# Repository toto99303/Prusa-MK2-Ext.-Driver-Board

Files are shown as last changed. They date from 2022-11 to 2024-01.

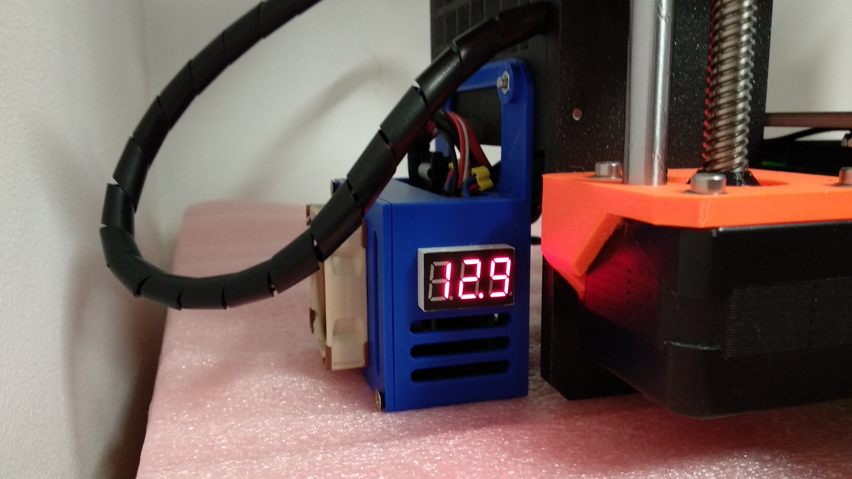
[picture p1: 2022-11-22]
Manuals/External driver board v2.4 (TMC2100, TMC2208, TMC2209))/high res pics/IMG_20180124_002903.jpg

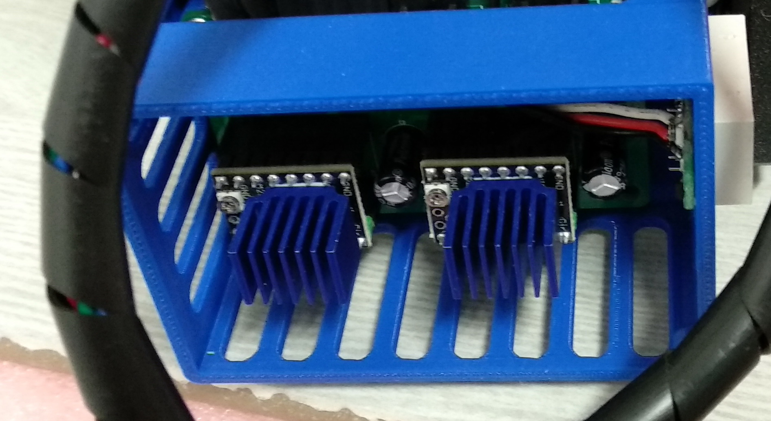
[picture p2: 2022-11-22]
Manuals/External driver board v2.1 with MK2.5/high res pics/drivers.jpg

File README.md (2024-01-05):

# Prusa-MK2-Ext.-Driver-Board
So, what is this? This is an external stepper driver board for X and Y stepper motors of the original Prusa MK2/MK2S/MK2.5/MK2.5S printers. It allows usage of TMC2100/TMC2208/TMC2209 drivers (Silent Step Stick and similar, (TMC2209 are recommended), so your printer will become a lot quieter and much smoother due to the 256 step interpolation (same as on the MK3). This is the latest upgraded version 2.4.1 of the board.  



More info here:  
https://vmod.wordpress.com/prusa-mk2s-ext-driver-board-v2-3/

BOM:

1 x wire-to-board header 3 POS 2.54MM(.100) (https://www.digikey.be/en/products/detail/cvilux-usa/CI3103P1V00-NH/13177511)

2 x 100uF 35V Capacitors (https://www.digikey.be/en/products/detail/rubycon/35ZLH100MEFC6-3X11/3134256)

2 x 10k through hole resistors (https://www.digikey.be/en/products/detail/stackpole-electronics-inc/RNF14BTE10K0/1682687)

1 x 2 way terminal block (https://www.tme.eu/en/details/dg306-5.0-2p12/pcb-terminal-blocks/degson-electronics/dg306-5-0-02p-12-00a-h/)

1 x right angle 2.54mm pin header 2x4 pins (https://jlcpcb.com/partdetail/Cvilux-CH81802H200/C918394)

2 x right angle dupont 1x4 MX2.54 TJC8 housing (https://vi.aliexpress.com/item/1005004362274135.html?gatewayAdapt=glo2vnm)

4 x driver header 1x8 2.54mm (https://grobotronics.com/pin-header-1x8-female-2.54mm.html?sl=en)

1 x IDC connector 2x4 wire-to-board connector (https://www.digikey.com/en/products/detail/cvilux-usa/CA2308PA10Z/15519128)

10-15cm short flat ribbon cable (https://www.digikey.com/en/products/detail/assmann-wsw-components/AWG28-16-G-300/655756)

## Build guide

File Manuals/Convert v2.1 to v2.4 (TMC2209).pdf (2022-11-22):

## Converting v2.1 to v2.4 and use TMC2209

When I created v2.1 there was no TMC2208 or TMC2209. It was designed for TMC2100.
That’s why you need to make some modifications to work with those.
I recommend buying TMC2209 in STANDALONE mode.

De-solder the jumpers (J_Y and J_X) on both boards and wire them as shown on the picture below:

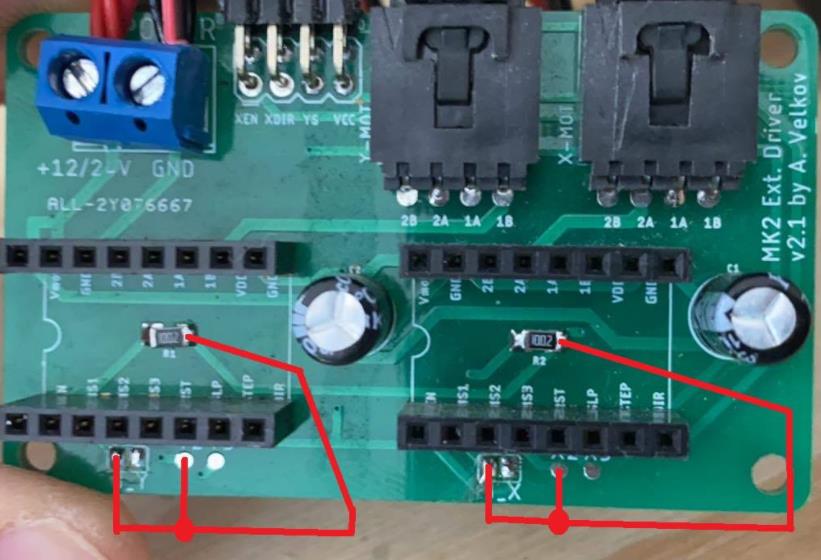
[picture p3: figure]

Be very careful and check everything with multimeter.
When done check for shorts between GND and VDC pin.

Next you need to cut the black cable connectors (Marked X Y Z etc.) from the gray data cable that go to mini-rambo and leave only the 8-pin connector going to the ext. driver board.
You will solder them to your mini-rambo later by the installation manual. They should look like this at the end:

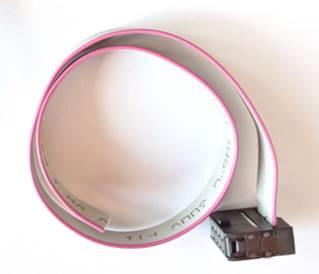
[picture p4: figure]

Next you need to follow the guide for v.2.4 here: https://drive.google.com/open?id=1o_A4ZHai253kLMRttBMnLbEIv-KRri8t

Also follow the manual for second board for Z axis if you have a second board.

One more important thing:

Most probably after plugging the board your motor axes will be inverted (X moving backwards instead of forward etc.).
If so you will need to swap the wires on each motor harness (X, Y). Use a needle and remove them carefully from the connector, swap them and plug them back:

So, we need to invert (switch) all wires on the X and Y motor connectors. Since connectors cannot be plugged in the opposite way you’ll have to use a small needle to pull all pins from the connectors and plug them back in reverse order:

### Original wiring: Left to right – Black, Green, Red, Blue

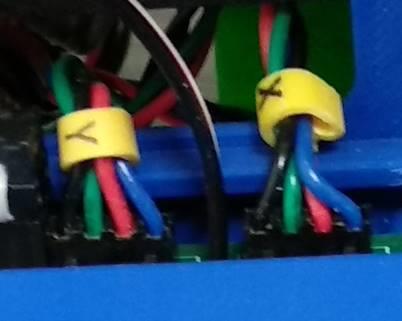
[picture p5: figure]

### New wiring: Left to right – Blue, Red, Green, Black

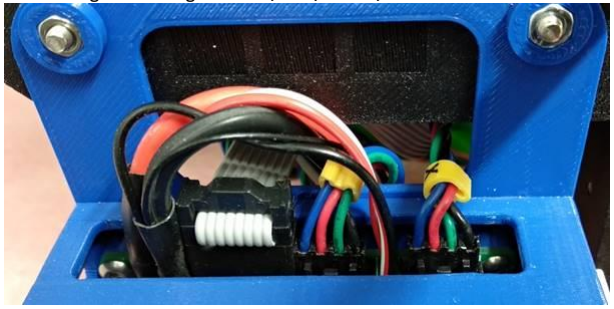
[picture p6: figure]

## Use needle here

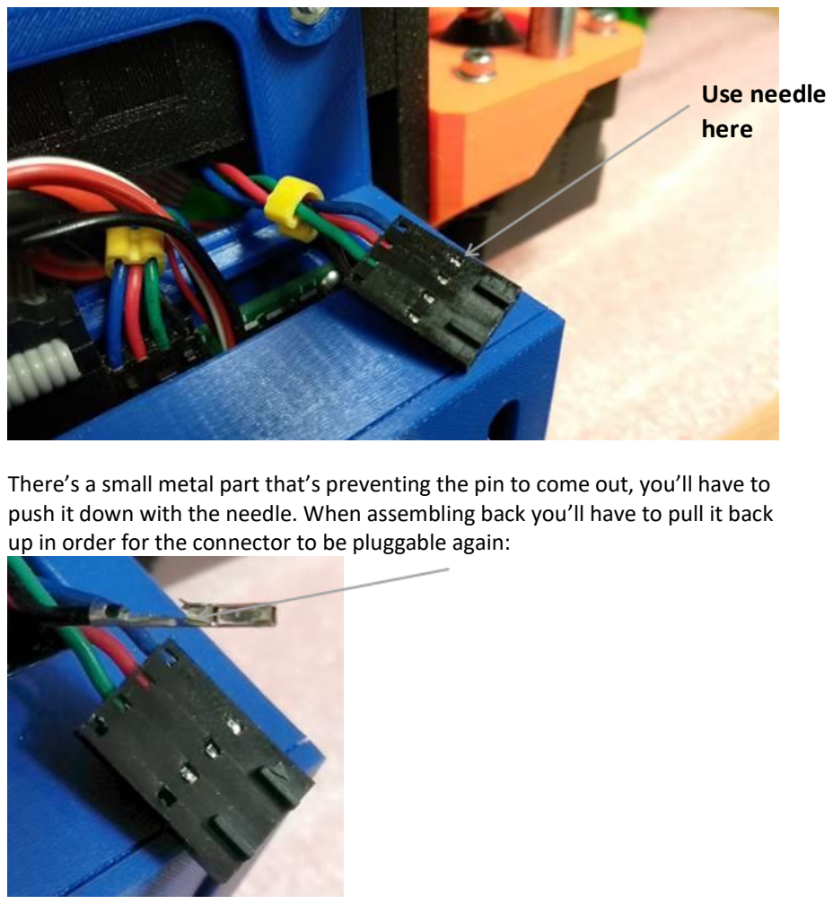
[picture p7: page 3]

### There’s a small metal part that’s preventing the pin to come out, you’ll have to push it down with the needle. When assembling back you’ll have to pull it back up in order for the connector to be pluggable again:

### Wire colors should look like this:

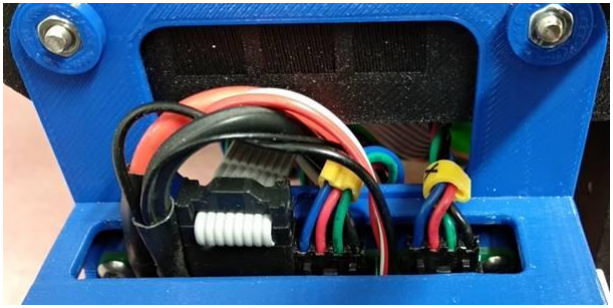
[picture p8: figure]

### That info should be enough for you to complete the mod with v2.1 and

TMC2209.

### Once again, read the manuals in advance, make a step-by-step plan and act

when ready and sure what you’re doing.

### I know it’s not an easy mod, but it’s worth it, believe me

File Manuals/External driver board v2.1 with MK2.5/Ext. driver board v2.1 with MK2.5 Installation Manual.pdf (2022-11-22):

## External Driver Board v2.1 with MK2.5 Installation Manual

Thanks for supporting this project! I’ll try to guide you as best as I can, but I will not go to the simple details as how to place the nuts on their place and put together a box, I assume you’re good enough to do this.

Ok, so you bought the old version of the ext. driver board (v2.1), but you want to install it with MK2.5 upgrade or any other current or future upgrade. This manual starts from the beginning but if you have it already installed you can skip some of the steps. Here’s two important things to know before proceeding with this mod:

1. By soldering on the back of your mini-rambo and changing motor connector pins you’re practically voiding your prusa warranty!
2. I take no responsibility if you mess this modification up and/or damage your printer. You need to have basic soldering skills. Do at your own risk, or get someone more experienced to do it for you!

Let’s start:
First you need to supply power to the board. You disassemble the original PSU plastic cover and take it out just a little up so you can connect the power leads to it:

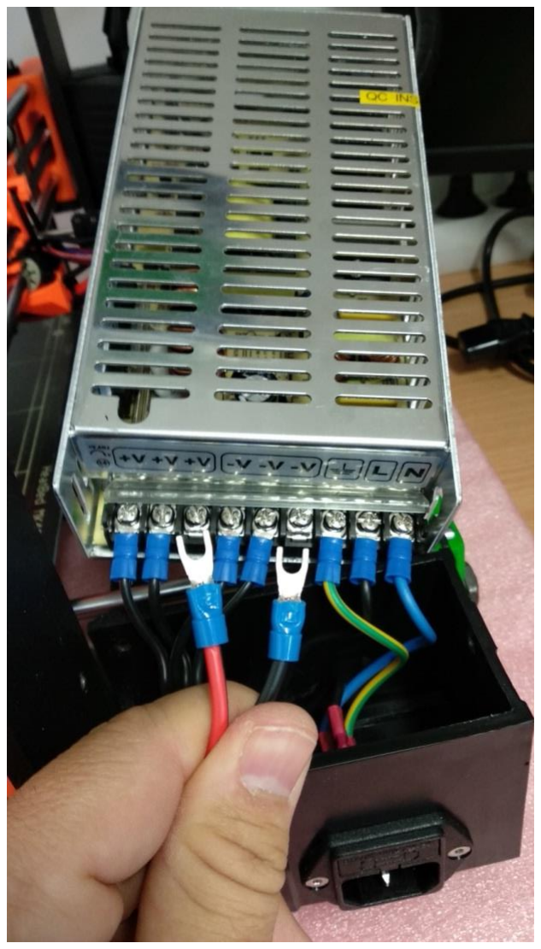
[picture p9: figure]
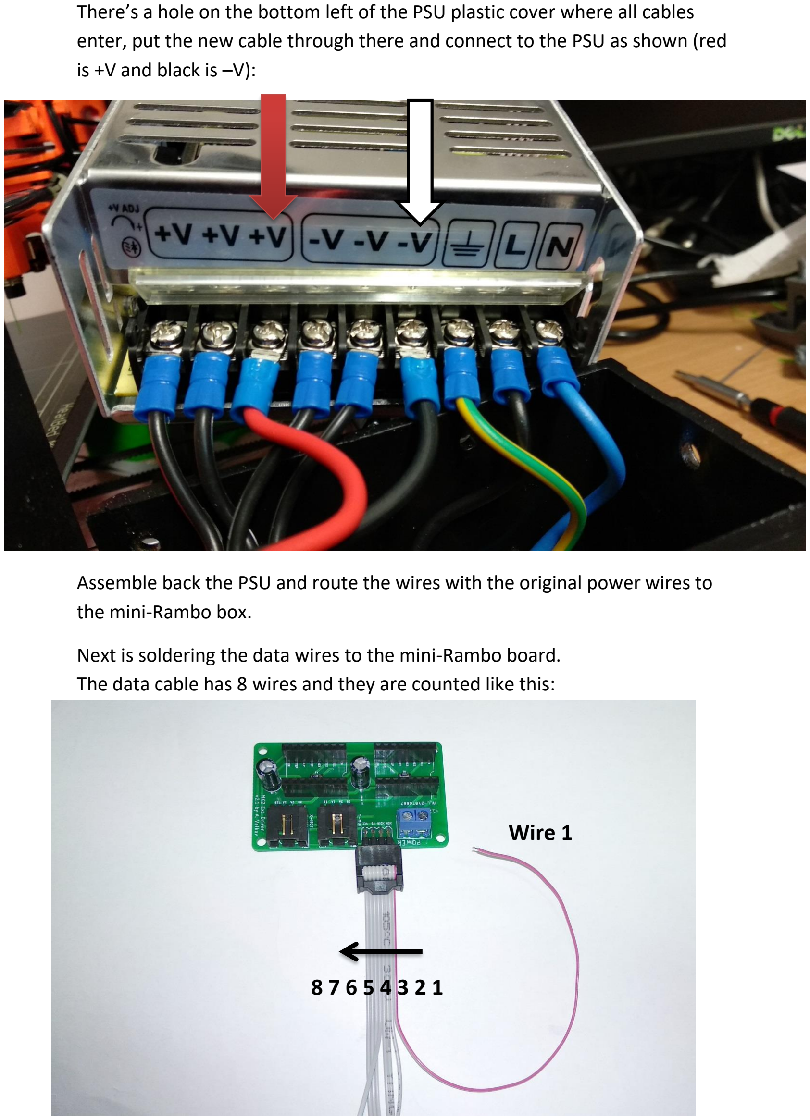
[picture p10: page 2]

There’s a hole on the bottom left of the PSU plastic cover where all cables enter, put the new cable through there and connect to the PSU as shown (red is +V and black is –V):

Assemble back the PSU and route the wires with the original power wires to the mini-Rambo box.

Next is soldering the data wires to the mini-Rambo board.
The data cable has 8 wires and they are counted like this:

8 7 6 5 4 3 2 1

Wire 1

Wires description:

The single wire on the side of the blue power connector is always wire number 1 (cable color could be red or grey)

1. X-EN - has to be soldered to XEN pad on the mini Rambo
2. X-STEP – has to be soldered to XSTEP pad on the mini Rambo
3. X-DIR – has to be soldered to XDIR pad on the mini Rambo
4. Y-EN – has to be soldered to YEN pad on the mini Rambo
5. Y-STEP - has to be soldered to YSTEP pad on the mini Rambo
6. Y-DIR - has to be soldered to YDIR pad on the mini Rambo
7. VCC - has to be soldered to +5V pad on the mini Rambo
8. GND - has to be soldered to GND pad on the mini Rambo

Unfortunately you will have to solder all 8 wires to the back of the mini-rambo.

In order to solder the wires you’ll have to unplug all cables and take the mini-rambo out of the box. Solder all wires on the back as shown below. (open the high res picture from the folder for clearer view)

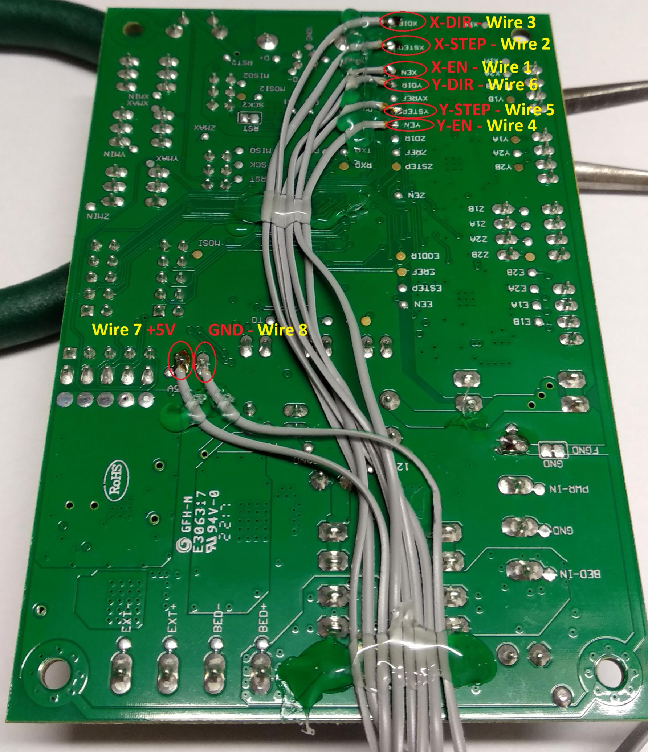
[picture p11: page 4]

Route all wires down and secure them with some hot silicone. This will prevent cutting the wires from vibrations etc.

You can now assemble the mini-rambo back in the original box with all cables plugged back (except for X and Y motor cables). Replace the bottom two screws with longer ones, remove the nuts from the original box and place them on the Ext. driver board box. (I assume you have printed it, https://www.thingiverse.com/thing:2777899) Assemble the external driver board in the new box and secure the box to the original box with the two longer screws. (note: If you’re installing a voltmeter place it first before the external board, otherwise it won’t be possible later) You should now have all data wires soldered, mini-rambo back in place with all cables plugged and the new box secured on the outside.

Now there’s one more thing you need to do. The new stepper drivers (TMC2100) have their motor direction naturally reversed with regards to the old drivers on the mini-rambo. So there’s two ways to fix this:

1. Use the original motor connector wiring and recompile the original prusa firmware with INVERT_X_DIR and INVERT_Y_DIR both set to “true” (located in Configuration.h)
2. Physically reverse the pins on the X and Y motor connectors and use the original untouched prusa firmware.

So for the first option, if you got this far you should already know how to compile and flash your own custom firmware. If not, let me know so I can send you the current re-compiled firmware for MK2.5 .

We’ll continue with the second option.

So, we need to invert (switch) all wires on the X and Y motor connectors. Since connectors cannot be plugged in the opposite way you’ll have to use a small needle to pull all pins from the connectors and plug them back in reverse order: Original wiring: Left to right – Black, Green, Red, Blue

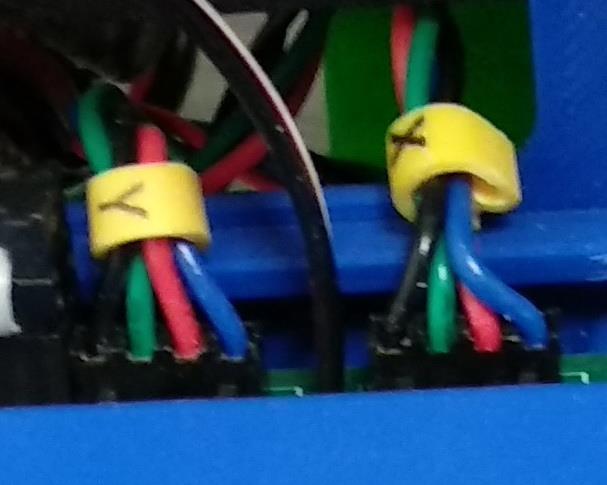
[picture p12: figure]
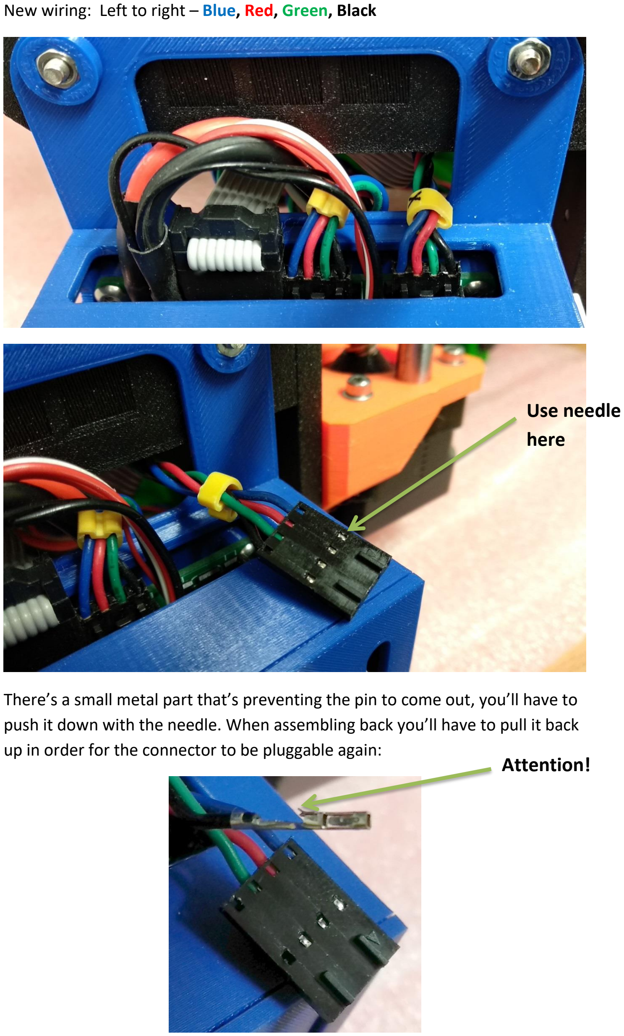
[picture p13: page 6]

New wiring: Left to right – Blue, Red, Green, Black

There’s a small metal part that’s preventing the pin to come out, you’ll have to push it down with the needle. When assembling back you’ll have to pull it back up in order for the connector to be pluggable again:

Use needle
here

Attention!

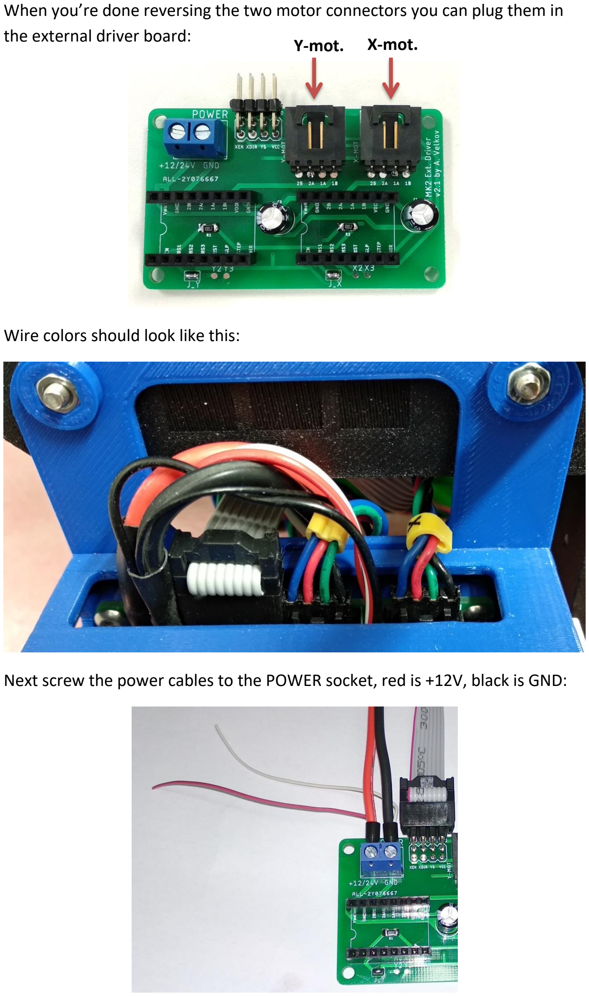
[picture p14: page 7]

When you’re done reversing the two motor connectors you can plug them in the external driver board:

Wire colors should look like this:

Next screw the power cables to the POWER socket, red is +12V, black is GND:

Y-mot. X-mot.

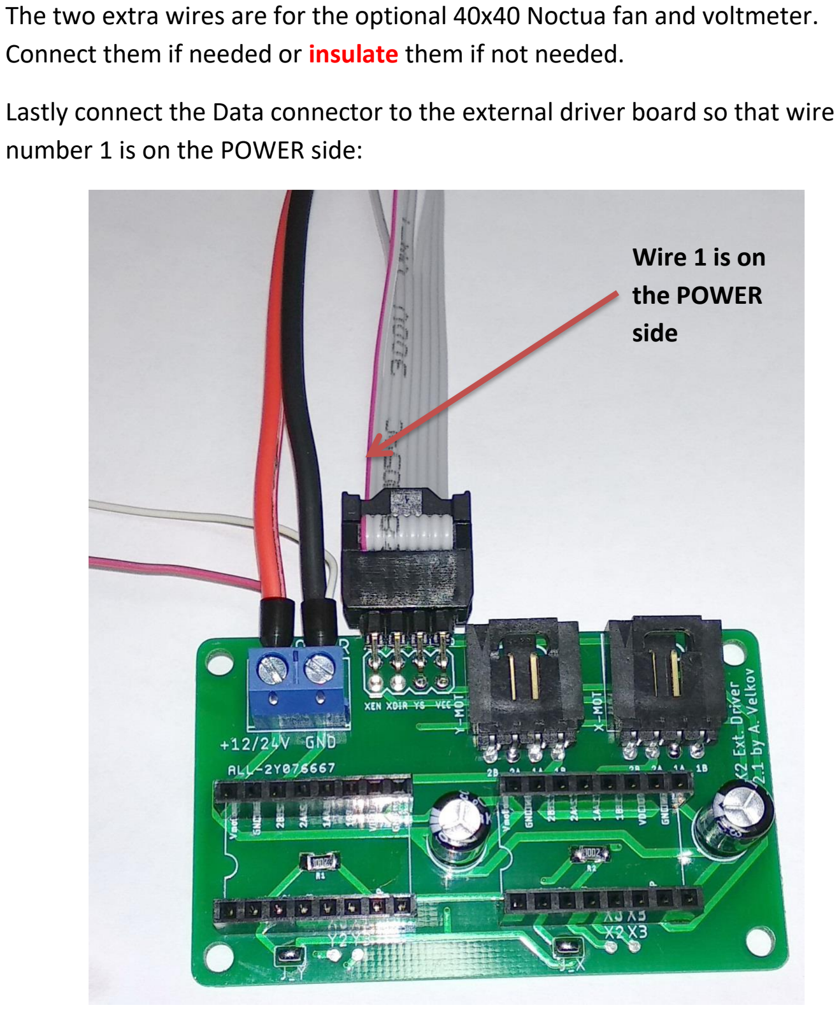
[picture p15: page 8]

The two extra wires are for the optional 40x40 Noctua fan and voltmeter. Connect them if needed or insulate them if not needed.

Lastly connect the Data connector to the external driver board so that wire number 1 is on the POWER side:

Wire 1 is on
the POWER
side

Now that you have all the wiring done you can plug the TMC2100 drivers to their places oriented with the pot trimmer on the left side:

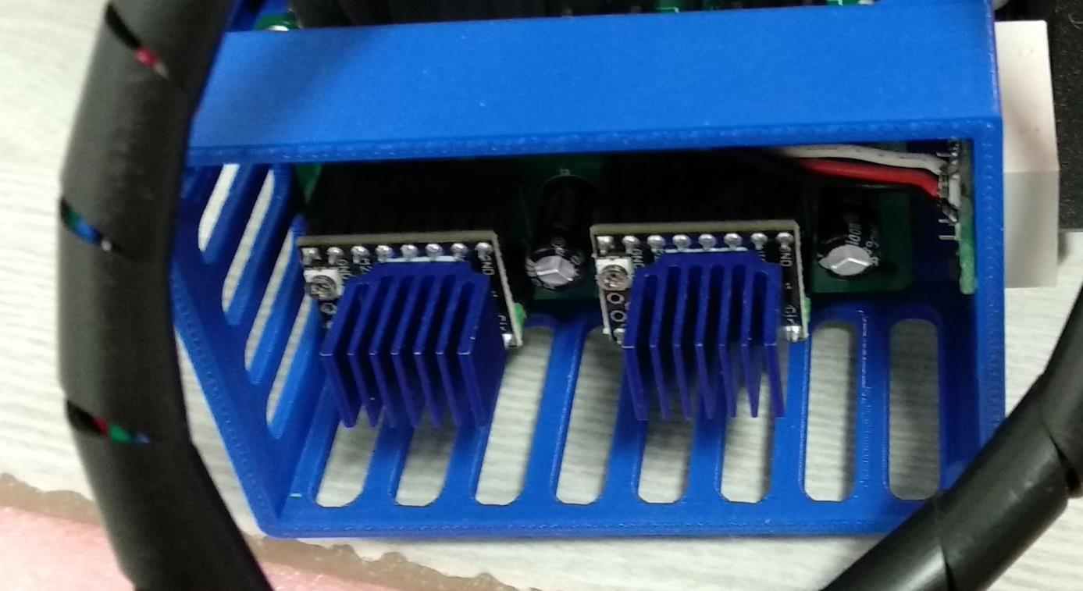
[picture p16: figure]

Check all wiring again before turning the printer on. Place bigger heatsinks if available on the drivers.

After powering on don’t rush to print, follow this first:

1. Check X and Y motors movement directions (Settings -> Move axis). Move them from the menu one by one. Are directions correct?
2. Check if “Disable steppers” is working fine.
3. Now you have to set Vref on the drivers, but it depends on what bearings you have on your Prusa. If you have LM8UU original bearings set Vref to 0.81V. If you use IGUS I recommend to set Vref to 1V or replace them back with the original metal ones, because IGUS will cause more friction and may cause layer shifting…
4. Set the Vref voltages on both drivers to 0.81 V with multimeter, here’s how:
- Put the multimeter to small DC voltage range (2 – 5 volts, etc.)
- Place the Black lead to GND on the POWER socket.
- Place the Red lead to the pot center or at the Vref pin if your driver has the pot on the bottom side.
- Rotate the pot with plastic screwdriver slowly clockwise so that voltage gets to 0.81 V. Stepper motors will get hot during print, but this seems to be normal for the TCM2100 drivers. Using plastic screwdriver will ensure you’re not going to short anything. I’ve already burned one driver with metal screwdriver…
5. Do XYZ calibration, and first layer calibration. (http://www.youtube.com/watch?v=JqH41K2vq0g&t=9m50s)

X and Y stepper movement should be normal and quieter than before.

Note that if you purchased original Watterott drivers they are configured by default for 1/16th SpreadCycle mode via the two jumpers on my board. You will probably hear whining or hissing in this mode.

To get the 1/16th StealthChop (silent) mode you have to desolder the X and Y jumpers here:

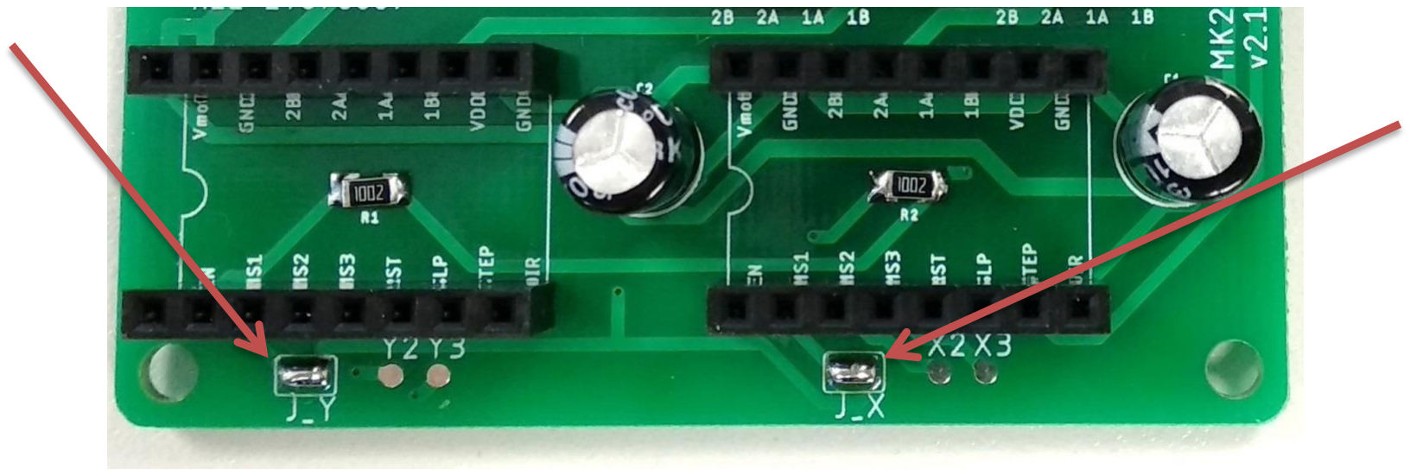
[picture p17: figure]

This is only for the original Watterott drivers.

If you purchased chinese clone drivers (MKS etc., black PCB) you’ll be already running in 1/16th StealthChop mode as those have their CGF pins floating and they are not affected by the jumpers on my board.

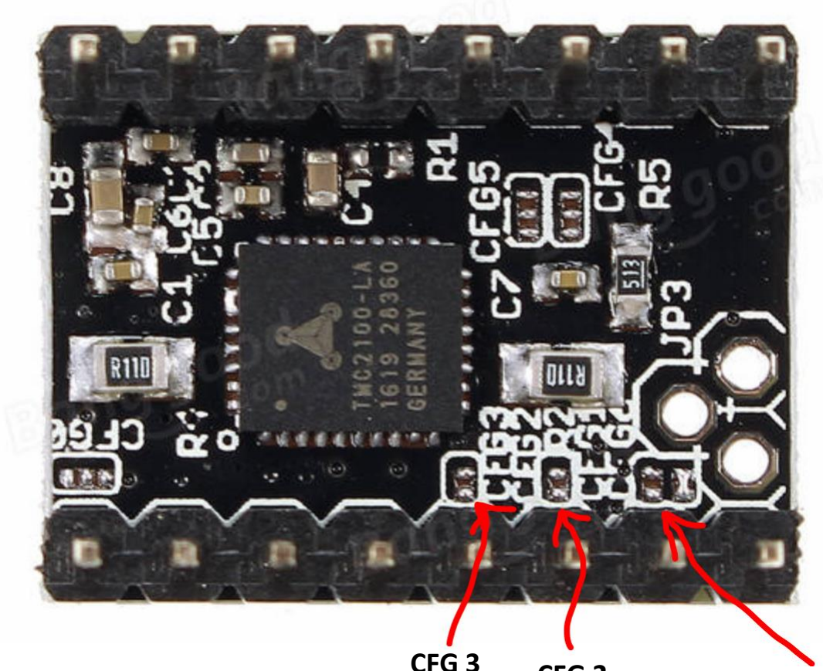
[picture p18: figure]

CFG 3 | CFG 2 | CFG 1

You can read more about this here: https://vmod.wordpress.com/2018/05/02/important-news-about-the-tmc2100-drivers/ (https://vmod.wordpress.com/2018/05/02/important-news-about-the-tmc2100-drivers/)

Before making the first print assemble the box cover with the optional Noctua fan. Cooling the drivers will be your second assurance for normal operation and no layer shifting.

Finally – enjoy your new silent MK2.5 printer! Happy printing!

Basic troubleshooting:

1. If X or Y motors are not moving you have a couple of reasons why:
- Check connection of wire 2 for X and wire 5 for Y.
- Check connection of wire 1 for X and wire 4 for Y.
- There’s no power to the external board, check the voltage on the power socket with multimeter (Red lead to 12V and Black to GND).
- There’s no 5V power to the stepper drivers, check wires 7 and 8. check the voltage between them with multimeter, should read 5V)
- Vref is too low. Set Vref according to the manual above.
- The stepper driver is faulty. I’ve seen this with some chinese clones. Turn the printer off and swap the two TMC2100s. If now the other axis is not moving then you have either wiring problem or driver is faulty.
2. “Disable steppers” is not working:
- Check connection of wire 1 for X and wire 4 for Y
3. Motor is moving only in one direction despite what you command from the LCD:
- Check connection of wire 3 for X and wire 6 for Y
4. XYZ calibration fails:
- Increase Vref with 0.5V on both stepper drivers. Repeat if it appears again.
5. Layer shift in X or Y axis:
- Check for hard movement on both directions.
- Increase Vref with 0.5V on the affected axis stepper driver. Repeat if it appears again.

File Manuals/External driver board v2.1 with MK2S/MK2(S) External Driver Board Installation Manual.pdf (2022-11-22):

## MK2(S) External Driver Board

## Installation Manual

Detailed features and description can be found on the blog page here: https://vmod.wordpress.com/prusa-mk2s-ext-driver-board/

Thanks for supporting this project! I’ll try to guide you as best as I can, but I will not go to the simple details as how to place the nuts on their place and put together a box, I assume you’re good enough to do this.

Let’s start:
First you need to supply power to the board. You disassemble the original PSU plastic cover and take it out just a little up so you can connect the power leads to it:

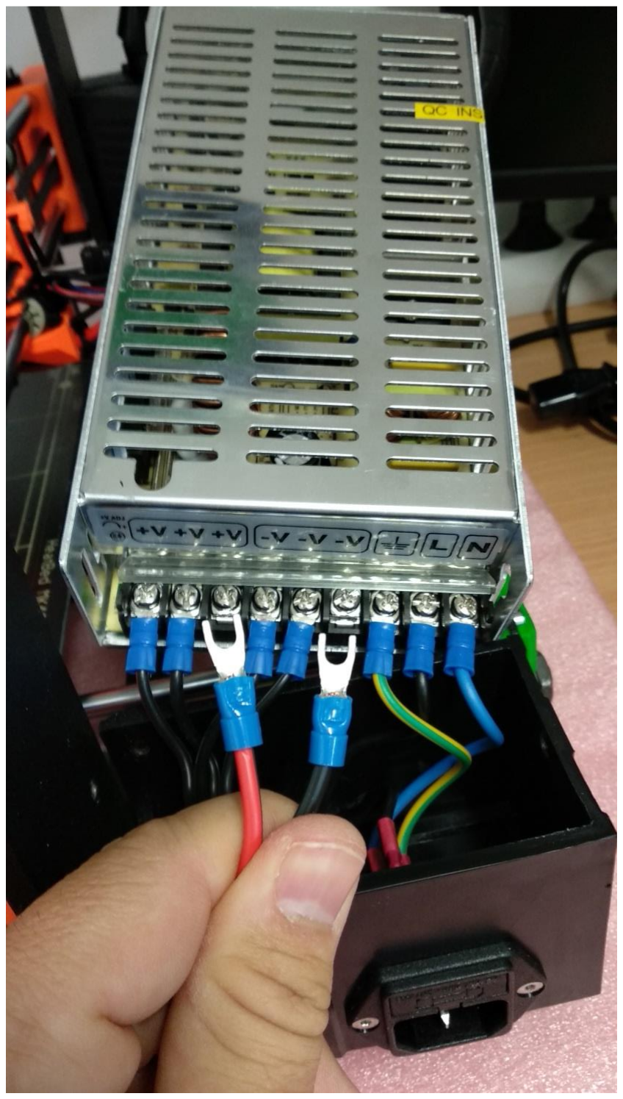
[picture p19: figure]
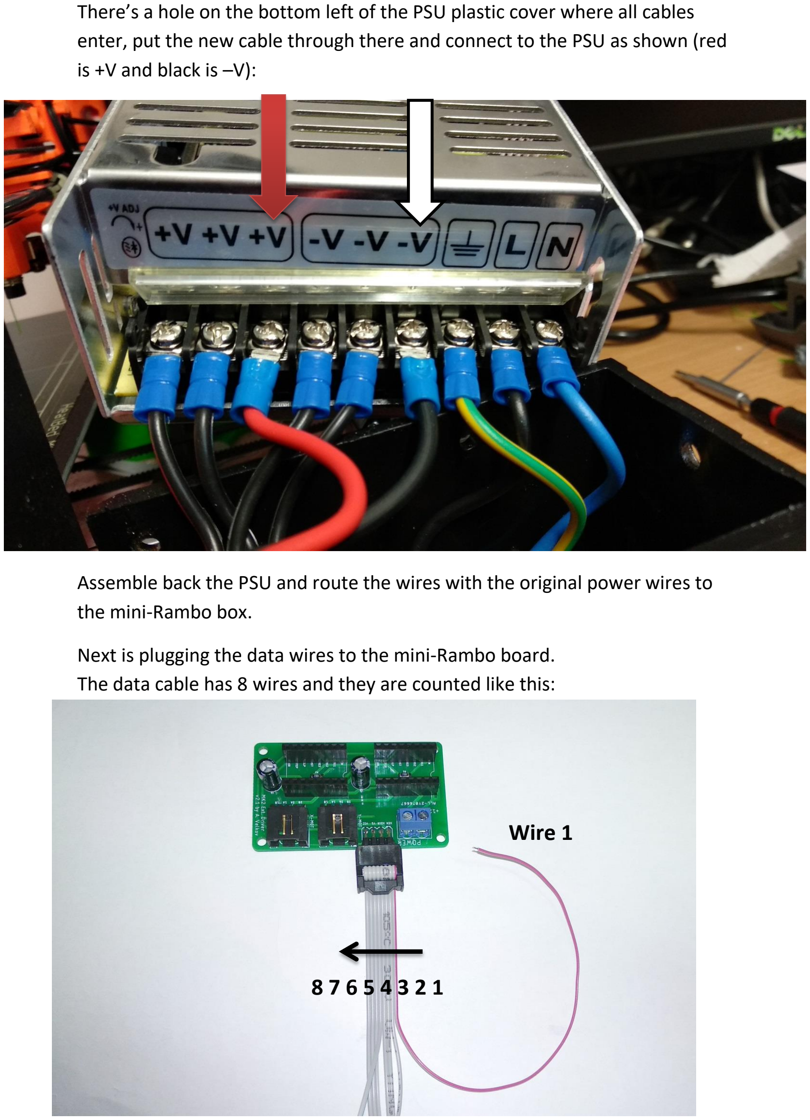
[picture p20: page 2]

There’s a hole on the bottom left of the PSU plastic cover where all cables enter, put the new cable through there and connect to the PSU as shown (red is +V and black is –V):

Assemble back the PSU and route the wires with the original power wires to the mini-Rambo box.

Next is plugging the data wires to the mini-Rambo board.
The data cable has 8 wires and they are counted like this:

8 7 6 5 4 3 2 1

Wire 1

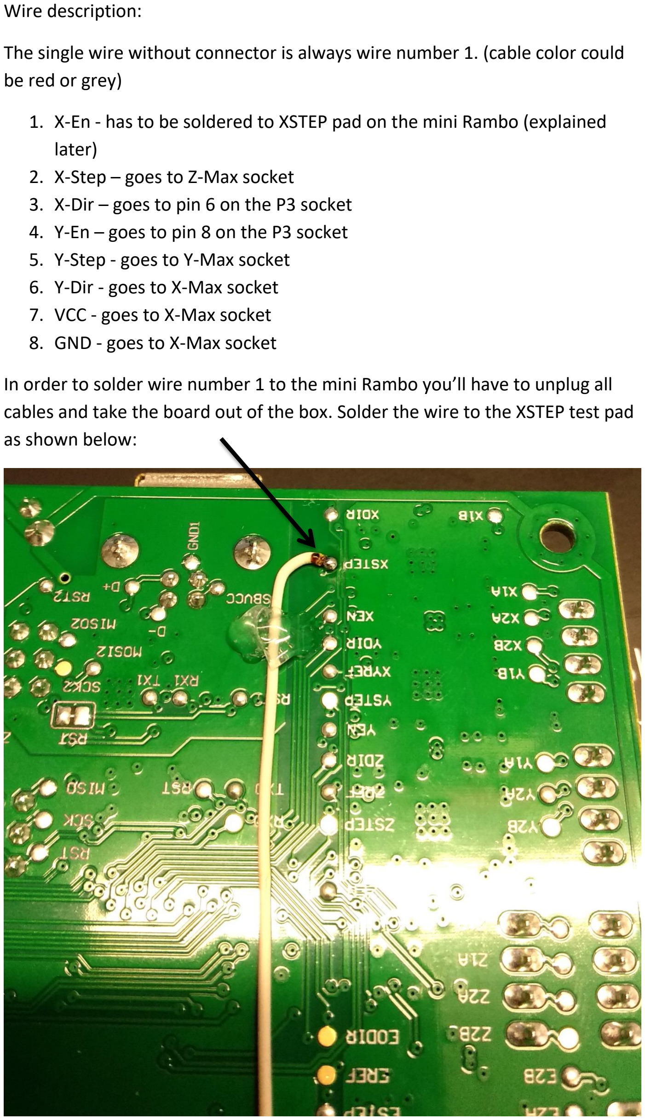
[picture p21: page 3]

Wire description:

The single wire without connector is always wire number 1. (cable color could be red or grey)

1. X-En - has to be soldered to XSTEP pad on the mini Rambo (explained later)
2. X-Step – goes to Z-Max socket
3. X-Dir – goes to pin 6 on the P3 socket
4. Y-En – goes to pin 8 on the P3 socket
5. Y-Step - goes to Y-Max socket
6. Y-Dir - goes to X-Max socket
7. VCC - goes to X-Max socket
8. GND - goes to X-Max socket

In order to solder wire number 1 to the mini Rambo you’ll have to unplug all cables and take the board out of the box. Solder the wire to the XSTEP test pad as shown below:

Route the wire down and secure it with some hot silicone. This will prevent cutting the wire from vibrations etc:

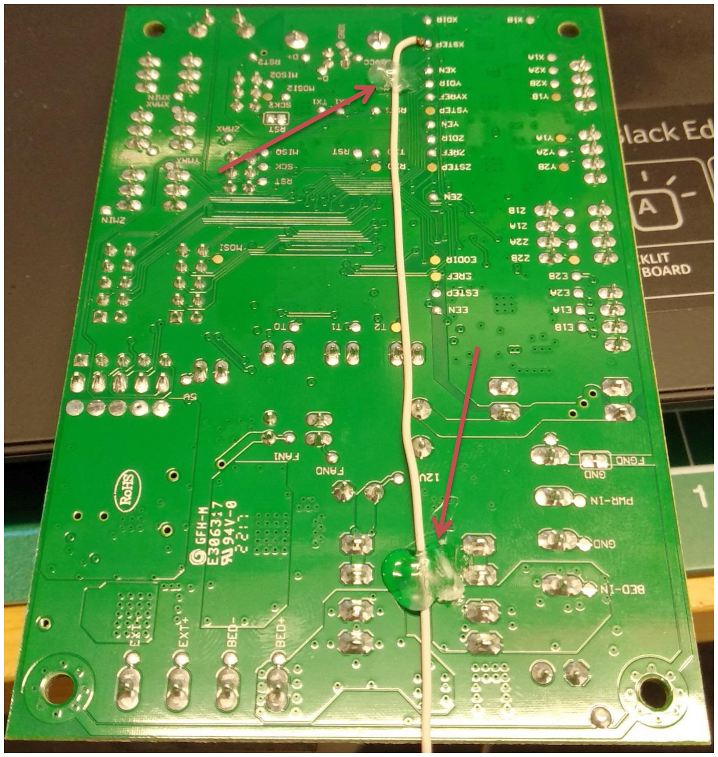
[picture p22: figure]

You can now assemble the mini-rambo back in the original box with all cables plugged back (except for X and Y motor cables). Replace the bottom two screws with longer ones, remove the nuts from the original box and place them on the Ext. driver board box. (I assume you have printed it, https://www.thingiverse.com/thing:2777899) Assemble the external driver board in the new box and secure the box to the original box with the two longer screws. (note: If you’re installing a voltmeter place it first before the external board, otherwise it won’t be possible later) You should now have wire number 1 soldered, mini-rambo back in place with all cables plugged and the new box secured on the outside with no cables plugged to the external driver board. We’ll plug them later.

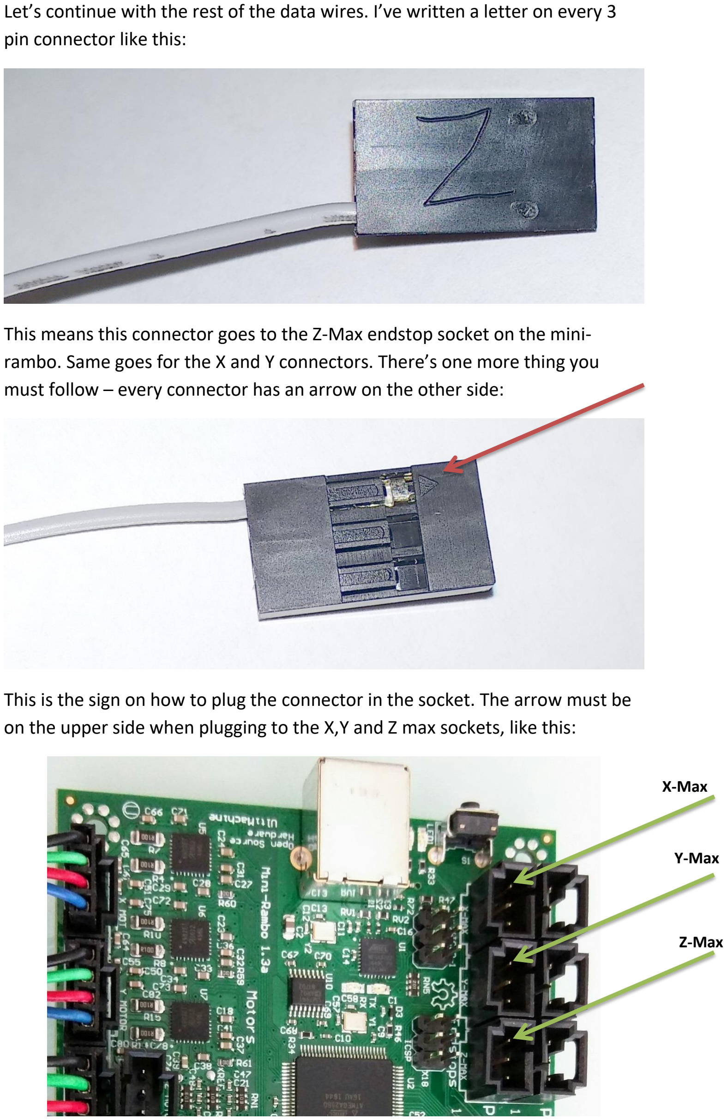
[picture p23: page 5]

Let’s continue with the rest of the data wires. I’ve written a letter on every 3 pin connector like this:

This means this connector goes to the Z-Max endstop socket on the mini-rambo. Same goes for the X and Y connectors. There’s one more thing you must follow – every connector has an arrow on the other side:

This is the sign on how to plug the connector in the socket. The arrow must be on the upper side when plugging to the X,Y and Z max sockets, like this:

X-Max

Z-Max

Y-Max

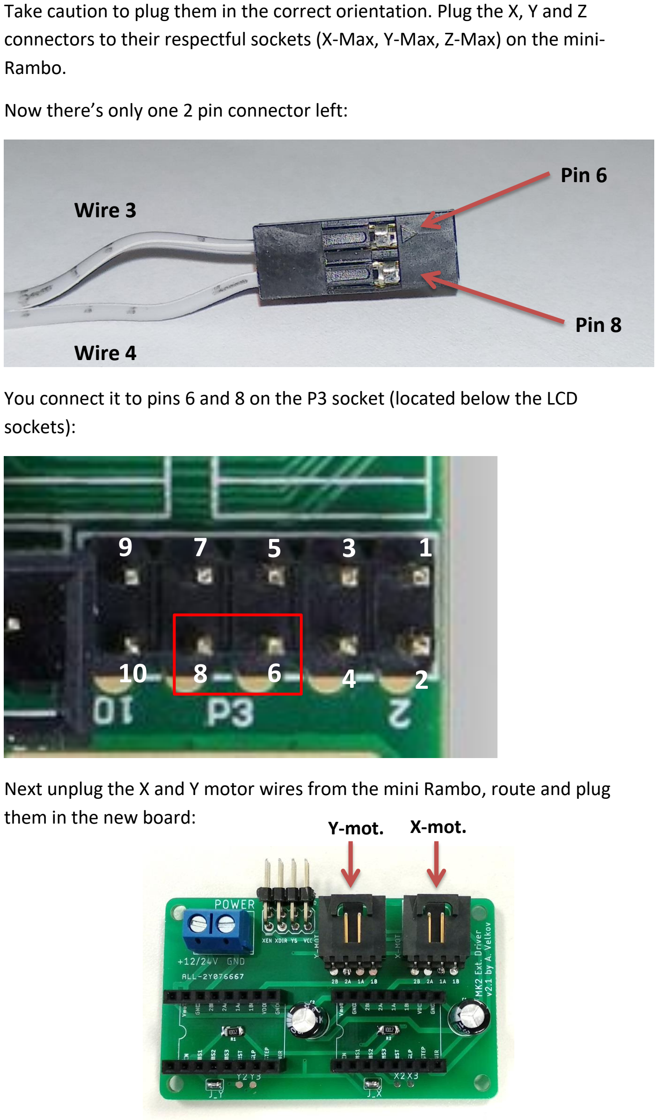
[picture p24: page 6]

Take caution to plug them in the correct orientation. Plug the X, Y and Z connectors to their respectful sockets (X-Max, Y-Max, Z-Max) on the mini-Rambo.

Now there’s only one 2 pin connector left:

You connect it to pins 6 and 8 on the P3 socket (located below the LCD sockets):

Next unplug the X and Y motor wires from the mini Rambo, route and plug them in the new board:

Wire 3

Wire 4

Pin 6

Pin 8

9 | 7 | 5 | 3 | 1

6 4
10 | 8 | 2
Y-mot. | X-mot.

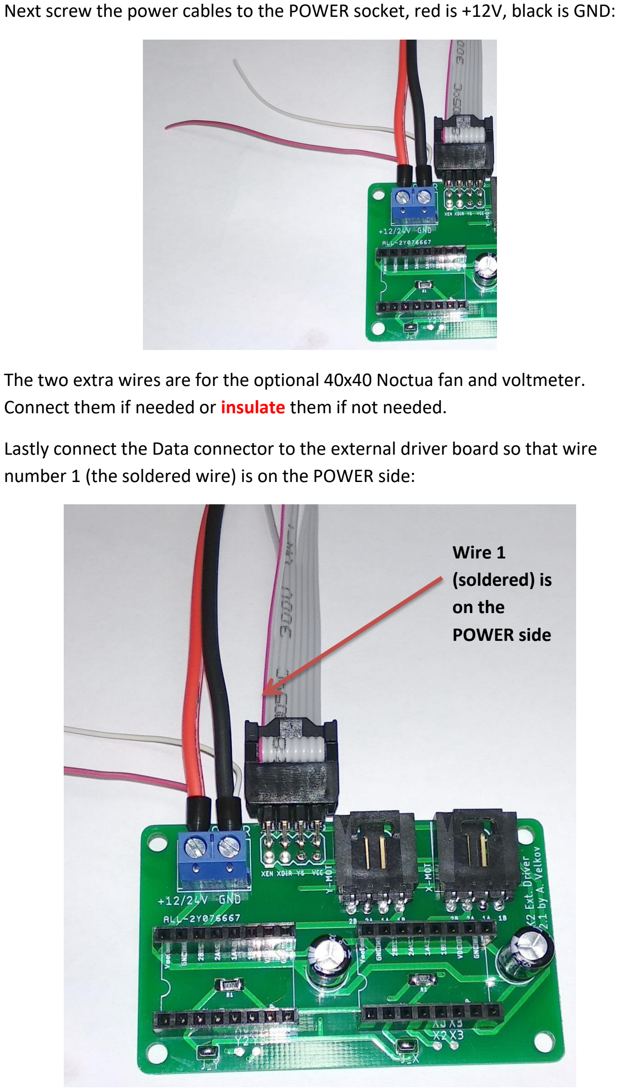
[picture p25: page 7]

Next screw the power cables to the POWER socket, red is +12V, black is GND:

The two extra wires are for the optional 40x40 Noctua fan and voltmeter. Connect them if needed or insulate them if not needed.

Lastly connect the Data connector to the external driver board so that wire number 1 (the soldered wire) is on the POWER side:

Wire 1
(soldered) is
on the
POWER side

Now that you have all the wiring done you can plug the TMC2100 drivers to their places oriented with the pot trimmer on the left side:

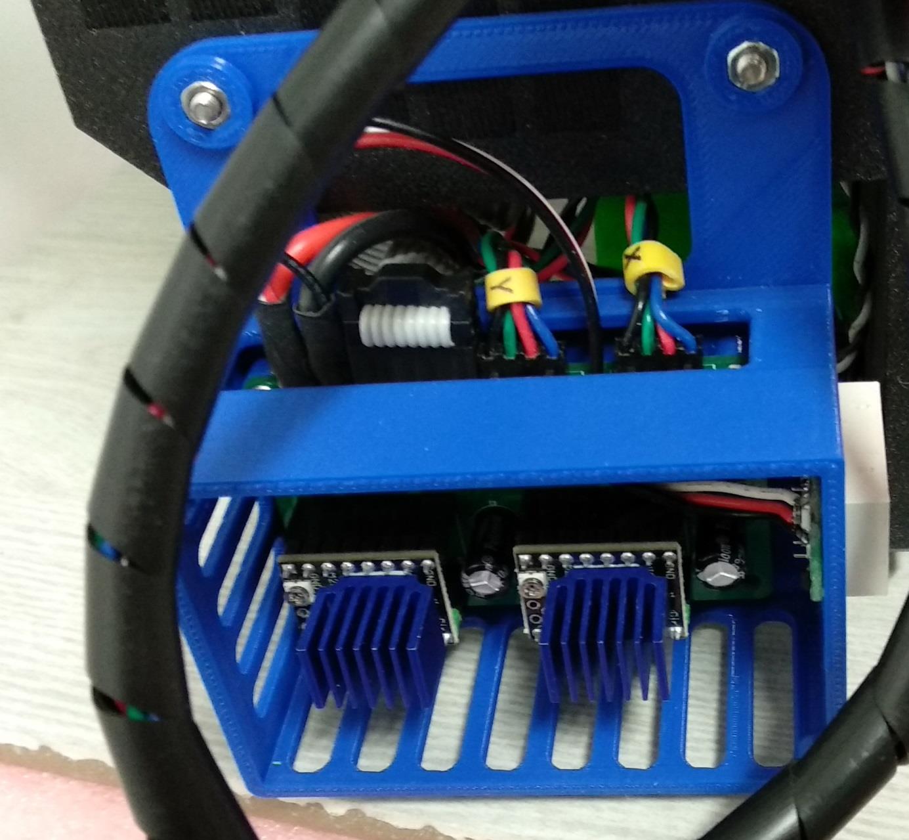
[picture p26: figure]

Everything should look like on the picture above. Check all wiring again before turning on the printer. Place bigger heatsinks if available on the drivers.

Now we’re ready to flash the modified firmware to the mini-Rambo. Download the ZIP file with the firmware from here (currently v3.1.0): https://drive.google.com/file/d/1ZUJ4TQwXW29yG_LHIU8oj9F0EPkxLeVB/view?usp=sharing (https://drive.google.com/file/d/1ZUJ4TQwXW29yG_LHIU8oj9F0EPkxLeVB/view?usp=sharing)

Inside you’ll find the original firmware for MMU and the standard printer and the modified ones for the external driver board. Turn on the printer and upload the desired firmware (in our case: 1_75mm_MK2-RAMBo13a-E3Dv6full_Ext_Driver_Board.hex) with the original Prusa Firmware Updater tool. You can follow the Prusa guide here (from Step 4):

http://help.prusa3d.com/l/en/article/r5ByKgVm69-firmware-upgrade-andflashing (http://help.prusa3d.com/l/en/article/r5ByKgVm69-firmware-upgrade-and-flashing)

After successful update don’t rush to print, follow this first:

1. Check X and Y motors movement directions (Settings -> Move axis). Move them from the menu one by one. Are directions correct?
2. Check if “Disable steppers” is working fine.
3. Set the Vref voltages on both drivers to 1V with multimeter, here’s how:
- Put the multimeter to small DC voltage range (2 – 5 volts, etc.)
- Place the Black lead to GND on the POWER socket.
- Place the Red lead to the pot center or at the Vref pin if your driver has the pot on the bottom side.
- Rotate the pot with plastic screwdriver so that voltage is 1V. I run mine at this voltage. Stepper motors will get hot during print, but this seems to be normal for the TCM2100 drivers. Using plastic screwdriver will ensure you’re not going to short anything. I’ve already burned one driver with metal screwdriver…
4. Do XYZ calibration, and first layer calibration. (http://www.youtube.com/watch?v=JqH41K2vq0g&t=9m50s)

X and Y stepper movement should be normal and quieter than before. The two drivers are configured by default for 1/16th SpreadCycle mode, which is the recommended one.

If you want to experiment you can turn on the 1/16th StealthChop mode by desoldering the X and Y jumpers here:

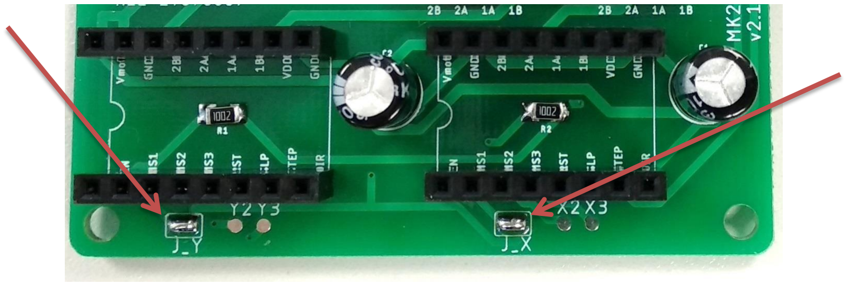
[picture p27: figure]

This will make it even quieter but will reduce the motor current and you might experience layer shifting. I don’t recommend this mode.

Before making the first print assemble the box cover with the optional Noctua fan. Cooling the drivers will be your second assurance for normal operation and no layer shifting.

Finally – enjoy your new silent MK2(S) printer! Happy printing!

Basic troubleshooting:

1. If X or Y motors are not moving you have a couple of reasons why:
- You have placed a connector the wrong way at the mini-rambo. Remember that the arrow on the connector should be on the upper side of the socket. Check again.
- There’s no power to the external board, check the voltage on the power socket with multimeter (Red lead to 12V and Black to GND).
- Vref is too low. Set Vref according to the manual above.
- The stepper driver is faulty. I’ve seen this with some chinese clones. Turn the printer off and swap the two TMC2100s. If now the other axis is not moving then you have either wiring problem or driver is faulty.
2. “Disable steppers” is not working:
- Check connection of wire 1 for X and wire 4 for Y
3. Motor is moving only in one direction despite what you command from the LCD:
- Check connection of wire 3 for X and wire 6 for Y

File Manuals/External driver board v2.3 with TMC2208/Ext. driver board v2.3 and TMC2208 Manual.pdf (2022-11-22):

## MK2(S) External Driver Board TMC2208 Installation Manual

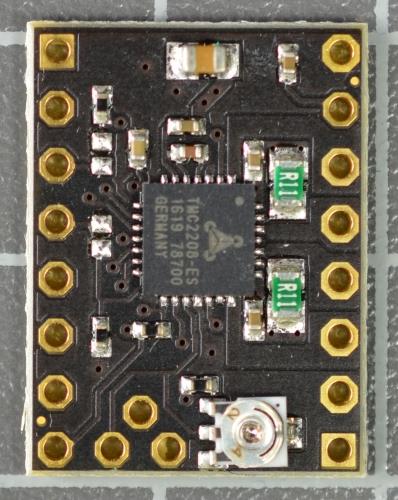
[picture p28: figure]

So, why using TMC2208? Mainly because:

stealthChop2™ No-noise, high-precision chopper algorithm for inaudible motion and inaudible standstill of the motor. Allows faster motor acceleration and deceleration than stealthChop™ and extends stealthChop to low stand still motor currents.
Benefits of using stealthChop2:
- Significantly improved microstepping with low cost motors
- Motor runs smooth and quiet
- Absolutely no standby noise
- Reduced mechanical resonance yields improved torque
- Reduced motor working temperature

Links:
https://www.watterott.com/index.php?page=product&info=5089 (without soldered pins)
https://www.watterott.com/en/SilentStepStick-TMC2208-with-Pins (with soldered pins)
https://www.watterott.com/en/Heatsink-9-x-9-x-12 (heatsinks)

Remark: the drivers from Watterott are being sold without heatsinks. You’ll have to buy them seperately.

WARNING!! I take no responsibility if you mess this modification up and/or damage your printer. You need to have basic soldering skills. Do at your own risk, or get someone more experienced to do it for you!

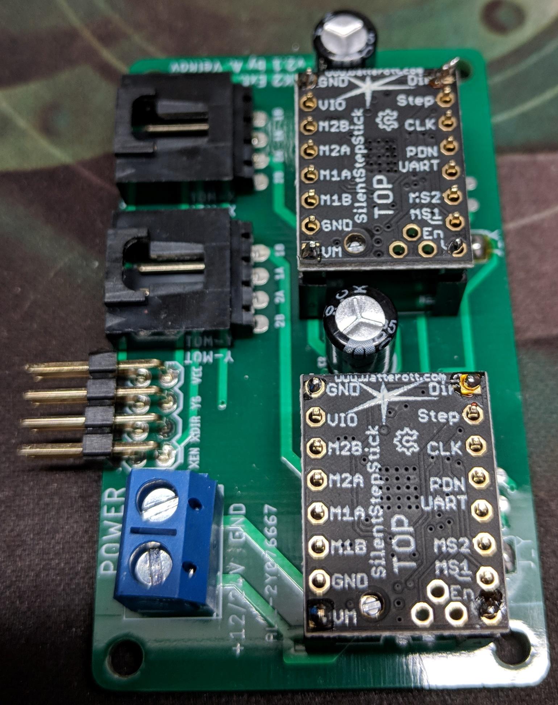
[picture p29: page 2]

Let’s start:
1. Make sure the printer is turned off. Remove the old TCM2100s from the external driver board. Remove the board from the box.
2. If you bought the drivers without pin headers the easiest way to solder them is to plug the headers in the sockets on the Ext. driver board and place the boards on top as shown (chip facing down) :

Now you can easily solder all the pins.

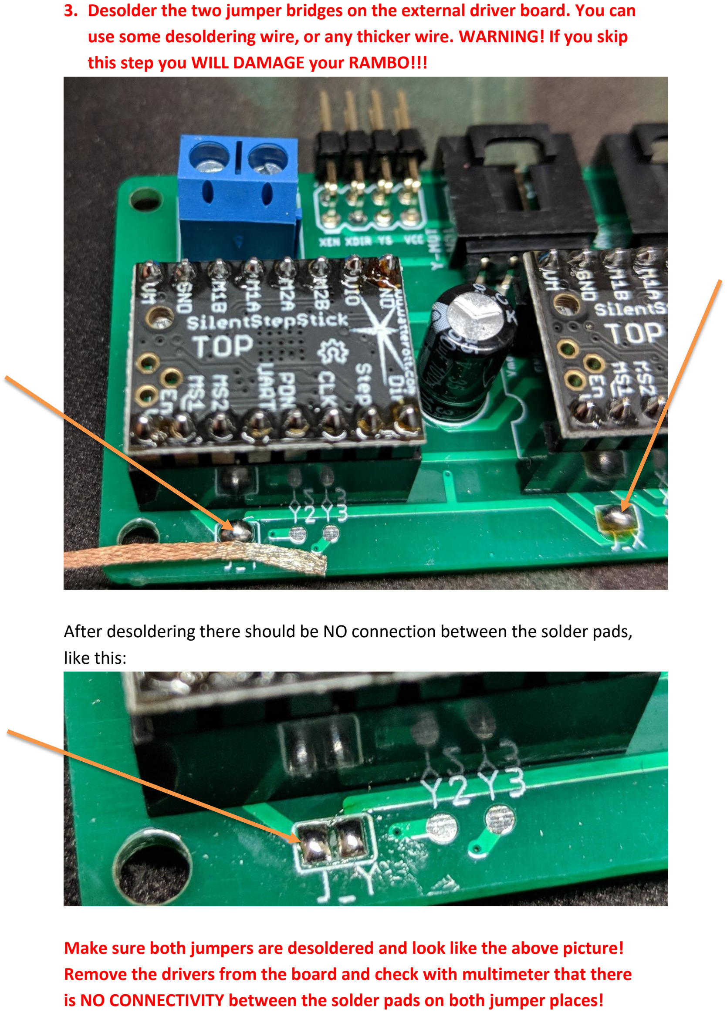
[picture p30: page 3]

### 3. Desolder the two jumper bridges on the external driver board. You can

use some desoldering wire, or any thicker wire. WARNING! If you skip this step you WILL DAMAGE your RAMBO!!!

After desoldering there should be NO connection between the solder pads, like this:

Make sure both jumpers are desoldered and look like the above picture! Remove the drivers from the board and check with multimeter that there is NO CONNECTIVITY between the solder pads on both jumper places!

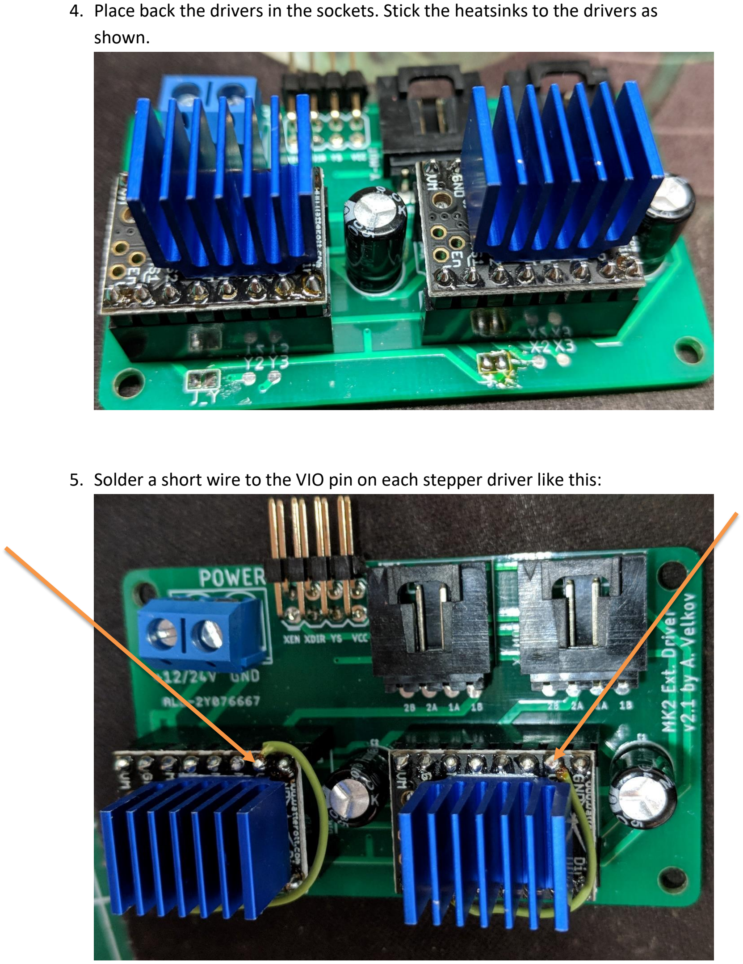
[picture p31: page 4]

4. Place back the drivers in the sockets. Stick the heatsinks to the drivers as shown.
5. Solder a short wire to the VIO pin on each stepper driver like this:

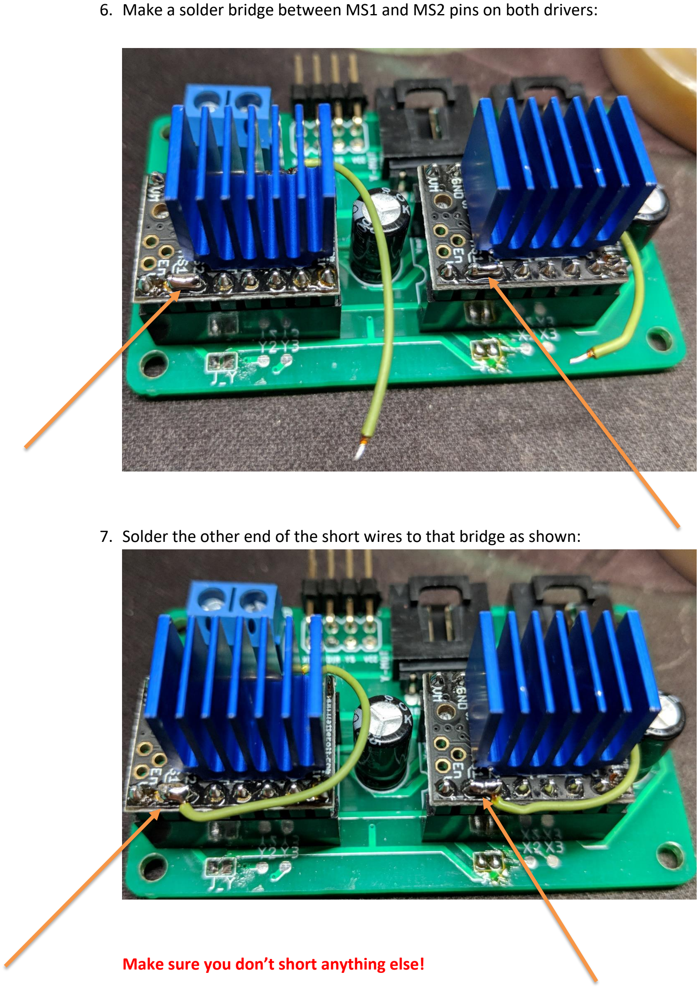
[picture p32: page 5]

6. Make a solder bridge between MS1 and MS2 pins on both drivers:
7. Solder the other end of the short wires to that bridge as shown:

Make sure you don’t short anything else!

8. Place the board back in the box and reconnect all wires. It should look like this:

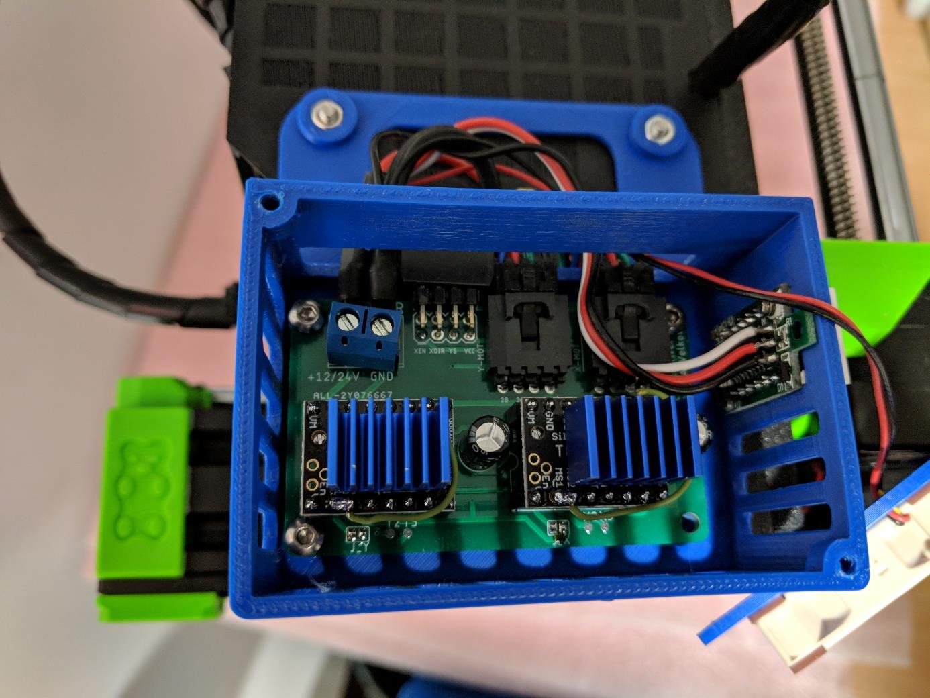
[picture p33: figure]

9. Check everything again (jumpers and solder bridges) and if you’re sure you did it fine you can turn on the printer.

After powering on don’t rush to print, follow this first:

1. Check X and Y motors movement directions (Settings -> Move axis). Move them from the menu one by one. Are directions correct?
2. Now you have to set Vref on the drivers, but it depends on what bearings you have on your Prusa. If you have LM8UU original bearings set Vref to 0.81V. If you use IGUS bearings I recommend to replace them back with the original metal ones, because IGUS will cause more friction and WILL cause layer shifting…
3. Set the Vref voltages on both drivers to 0.81 V with multimeter, here’s how:
- Put the multimeter to small DC voltage range (2 – 5 volts, etc.)
- Place the Black lead to GND on the POWER socket.
- Place the Red lead to the pin close to the En pin on each driver:

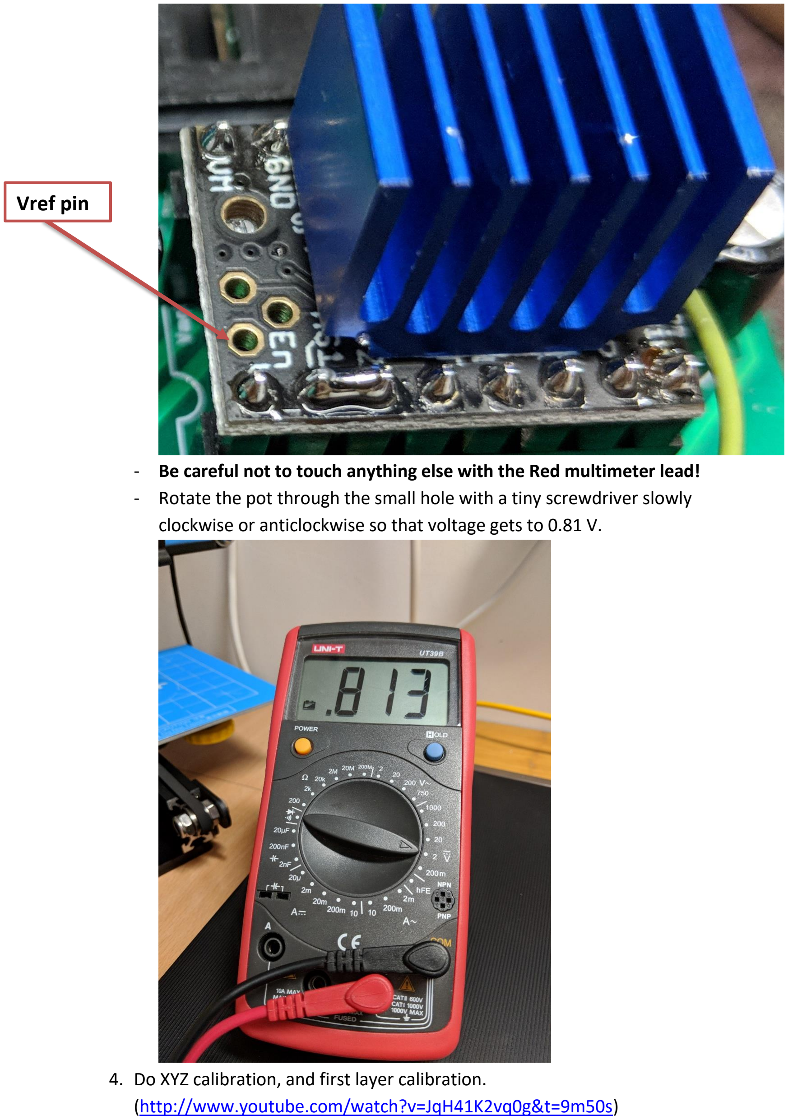
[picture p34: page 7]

- Be careful not to touch anything else with the Red multimeter lead!
- Rotate the pot through the small hole with a tiny screwdriver slowly clockwise or anticlockwise so that voltage gets to 0.81 V.
4. Do XYZ calibration, and first layer calibration. (http://www.youtube.com/watch?v=JqH41K2vq0g&t=9m50s)

Vref pin

5. Enjoy your even more quiet printer!

Troubleshooting:

1. XYZ calibration fails:
- Increase Vref with 0.05V on both stepper drivers. Repeat if it appears again.
2. Layer shift in X or Y axis:
- Check for hard movement on both directions.
- Increase Vref with 0.05V on the affected axis stepper driver. Repeat if it appears again.

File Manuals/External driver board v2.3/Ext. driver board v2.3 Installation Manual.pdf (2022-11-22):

## MK2(S) External Driver Board v2.3 Installation Manual

Thanks for supporting this project! I’ll try to guide you as best as I can, but I will not go to the simple details as how to place the nuts on their place and put together a box, I assume you’re good enough to do this.

Here’s two important things to know before proceeding with this mod:

1. By soldering on the back of your mini-rambo you’re practically voiding your prusa warranty!
2. I take no responsibility if you mess this modification up and/or damage your printer. You need to have basic soldering skills. Do at your own risk, or get someone more experienced to do it for you!

Let’s start:
First you need to supply power to the board. You disassemble the original PSU plastic cover and take it out just a little up so you can connect the power leads to it:

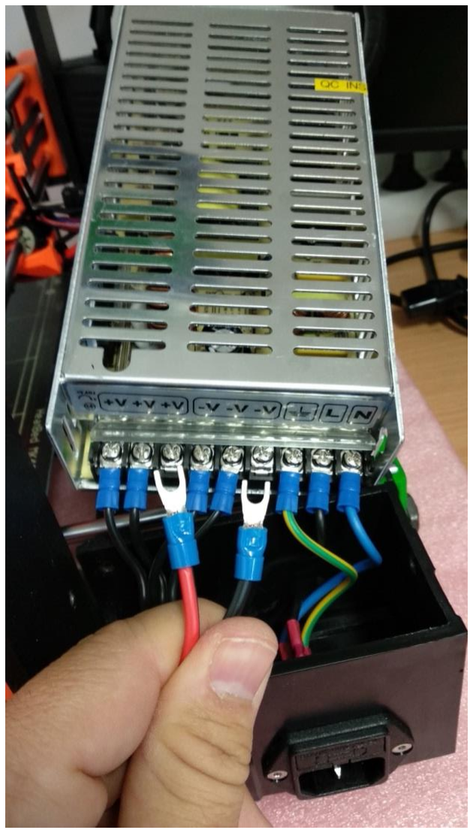
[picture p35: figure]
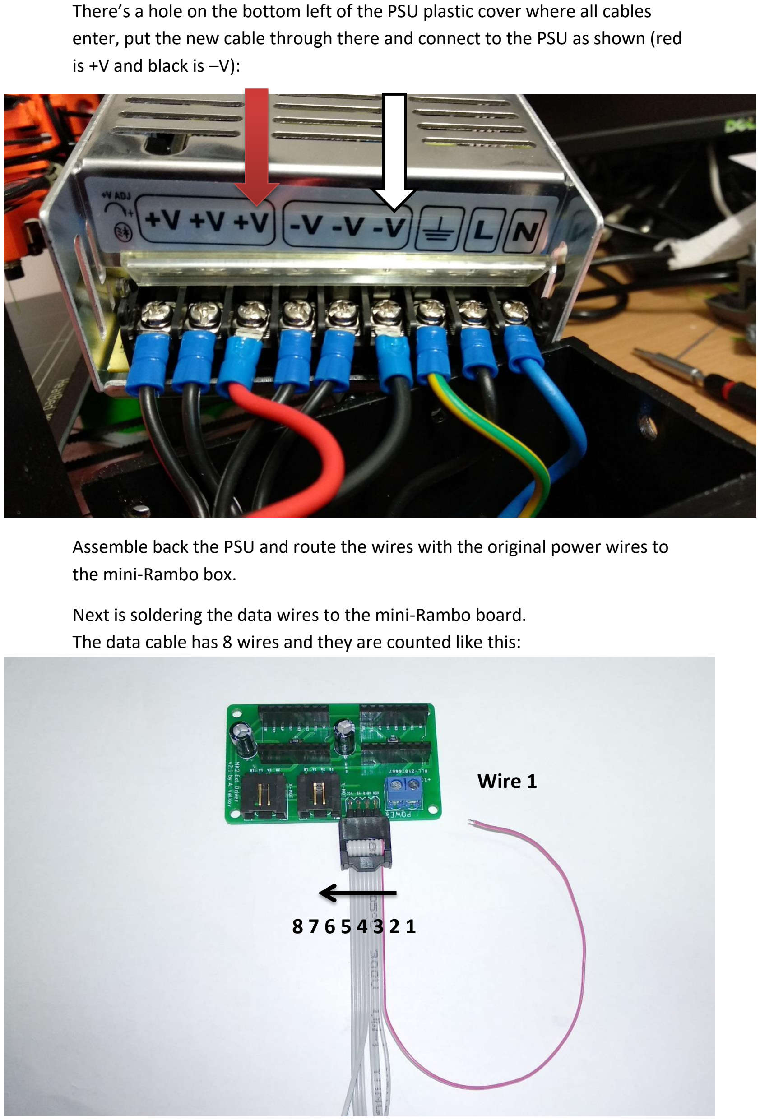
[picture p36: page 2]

There’s a hole on the bottom left of the PSU plastic cover where all cables enter, put the new cable through there and connect to the PSU as shown (red is +V and black is –V):

Assemble back the PSU and route the wires with the original power wires to the mini-Rambo box.

Next is soldering the data wires to the mini-Rambo board.
The data cable has 8 wires and they are counted like this:

8 7 6 5 4 3 2 1

Wire 1

Wires description:

The wire on the side of the blue power connector is always wire number 1 (cable color could be red or grey)

1. X-EN - has to be soldered to XEN pad on the mini Rambo
2. X-STEP – has to be soldered to XSTEP pad on the mini Rambo
3. X-DIR – has to be soldered to XDIR pad on the mini Rambo
4. Y-EN – has to be soldered to YEN pad on the mini Rambo
5. Y-STEP - has to be soldered to YSTEP pad on the mini Rambo
6. Y-DIR - has to be soldered to YDIR pad on the mini Rambo
7. VCC - has to be soldered to +5V pad on the mini Rambo
8. GND - has to be soldered to GND pad on the mini Rambo

Unfortunately you will have to solder all 8 wires to the back of the mini-rambo.

Carefully peel off all 8 wires of the data cable almost to the end of the cable. Length should be enough to reach the solder points on the mini-rambo. Tin all wire ends and cut the excess wire so that you end up with very short tinned end.

In order to solder the wires you’ll have to unplug all cables and take the mini-rambo out of the box. Solder all wires on the back as shown below. (open the high res picture from the folder for clearer view)


Route all wires down and secure them with some hot silicone. This will prevent cutting the wires from vibrations etc.

You can now assemble the mini-rambo back in the original box with all cables plugged back (except for X and Y motor cables). Replace the bottom two screws with longer ones, remove the nuts from the original box and place them on the Ext. driver board box. (I assume you have printed it, https://www.thingiverse.com/thing:2777899) Assemble the external driver board in the new box and secure the box to the original box with the two longer screws. (note: If you’re installing a voltmeter place it first before the external board, otherwise it won’t be possible later) You should now have all data wires soldered, mini-rambo back in place with all cables plugged and the new box secured on the outside.

You can now plug motor cables for X and Y motors in the external driver board:

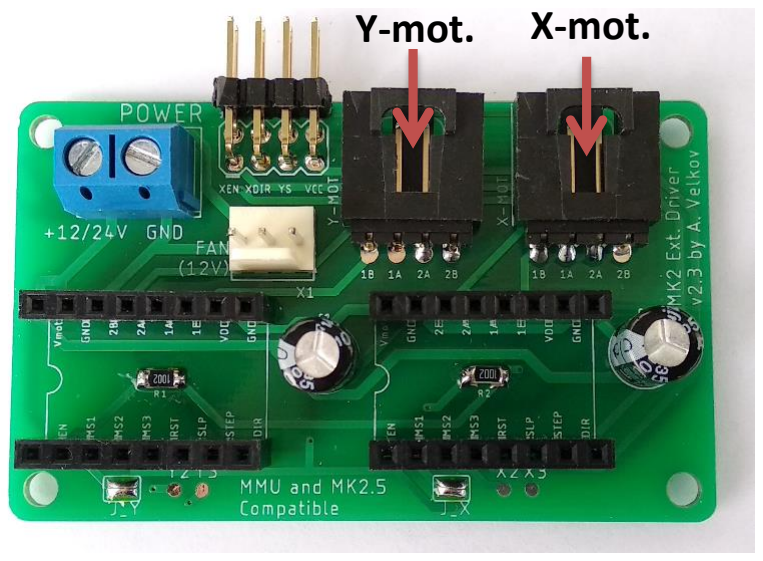
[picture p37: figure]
Y-mot.; X-mot.

Next screw the power cables to the POWER socket, red is +12V, black is GND:

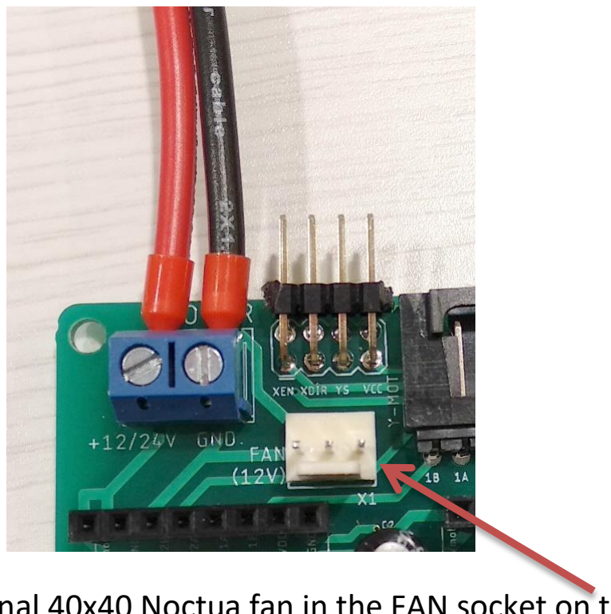
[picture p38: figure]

You can plug the optional 40x40 Noctua fan in the FAN socket on the board.

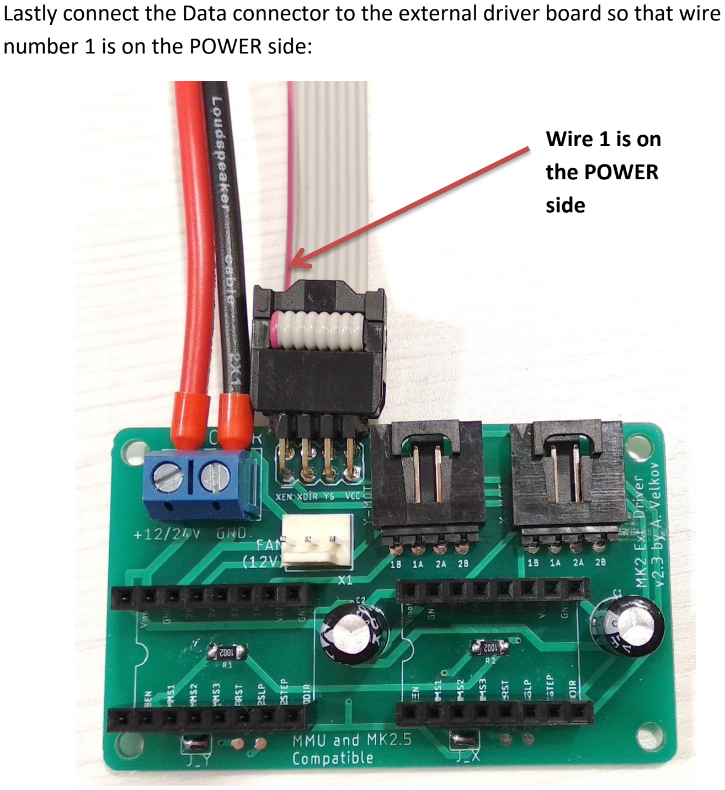
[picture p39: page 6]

Lastly connect the Data connector to the external driver board so that wire number 1 is on the POWER side:

Wire 1 is on
the POWER
side

Now that you have all the wiring done you can plug the TMC2100 drivers to their places oriented with the pot trimmer on the left side:


Check all wiring again before turning the printer on. Place bigger heatsinks if available on the drivers.

After powering on don’t rush to print, follow this first:

1. Check X and Y motors movement directions (Settings -> Move axis). Move them from the menu one by one. Are directions correct?
2. Check if “Disable steppers” is working fine.
3. Now you have to set Vref on the drivers, but it depends on what bearings you have on your Prusa. If you have LM8UU original bearings set Vref to 0.81V. If you use IGUS I recommend to set Vref to 1V or replace them back with the original metal ones, because IGUS will cause more friction and may cause layer shifting…
4. Set the Vref voltages on both drivers to 0.81 V with multimeter, here’s how:
- Put the multimeter to small DC voltage range (2 – 5 volts, etc.)
- Place the Black lead to GND on the POWER socket.
- Place the Red lead to the pot center or at the Vref pin if your driver has the pot on the bottom side.
- Rotate the pot with plastic screwdriver slowly clockwise so that voltage gets to 0.81 V. Stepper motors will get hot during print, but this seems to be normal for the TCM2100 drivers. Using plastic screwdriver will ensure you’re not going to short anything. I’ve already burned one driver with metal screwdriver…
5. Do XYZ calibration, and first layer calibration. (http://www.youtube.com/watch?v=JqH41K2vq0g&t=9m50s)

X and Y stepper movement should be normal and quieter than before.

Note that if you purchased original Watterott drivers they are configured by default for 1/16th SpreadCycle mode via the two jumpers on my board. You will probably hear whining or hissing in this mode.

To get the 1/16th StealthChop (silent) mode you have to desolder the X and Y jumpers here:

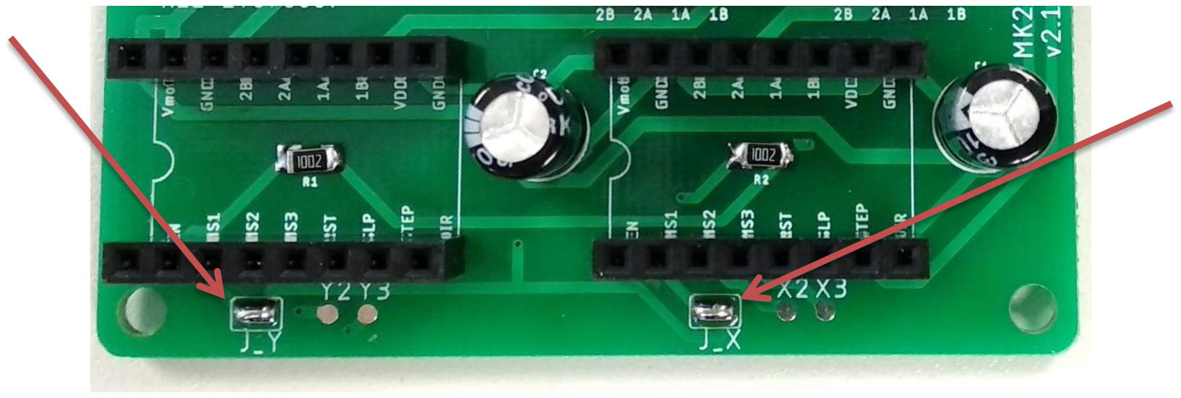
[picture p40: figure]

This is only for the original Watterott drivers.

If you purchased chinese clone drivers (MKS etc., black PCB) you’ll be already running in 1/16th StealthChop mode as those have their CGF pins floating and they are not affected by the jumpers on my board.

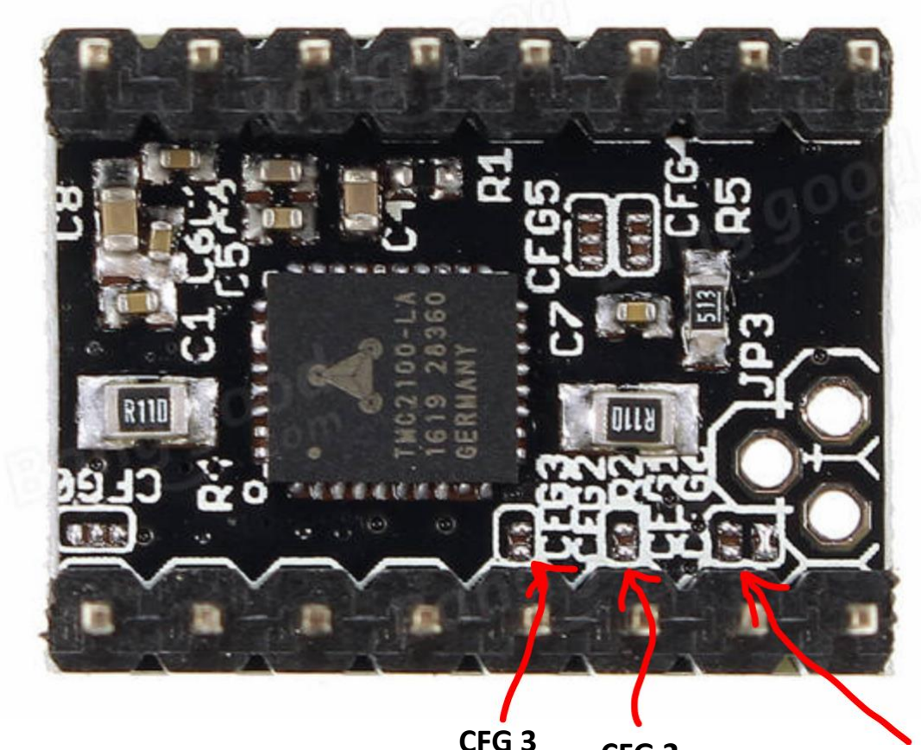
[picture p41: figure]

CFG 3 | CFG 2 | CFG 1

You can read more about this here: https://vmod.wordpress.com/2018/05/02/important-news-about-thetmc2100-drivers/ (https://vmod.wordpress.com/2018/05/02/important-news-about-the-tmc2100-drivers/)

Before making the first print assemble the box cover with the optional Noctua fan. Cooling the drivers will be your second assurance for normal operation and no layer shifting.

Finally – enjoy your new silent printer! Happy printing!

Basic troubleshooting:

1. If X or Y motors are not moving you have a couple of reasons why:
- Check connection of wire 2 for X and wire 5 for Y.
- Check connection of wire 1 for X and wire 4 for Y.
- There’s no power to the external board, check the voltage on the power socket with multimeter (Red lead to 12V and Black to GND).
- There’s no 5V power to the stepper drivers, check wires 7 and 8. check the voltage between them with multimeter, should read 5V)
- Vref is too low. Set Vref according to the manual above.
- The stepper driver is faulty. I’ve seen this with some Chinese clones. Turn the printer off and swap the two TMC2100s. If now the other axis is not moving then you have either wiring problem or driver is faulty.
2. “Disable steppers” is not working:
- Check connection of wire 1 for X and wire 4 for Y
3. Motor is moving only in one direction despite what you command from the LCD:
- Check connection of wire 3 for X and wire 6 for Y
4. XYZ calibration fails:
- Increase Vref with 0.05V on both stepper drivers. Repeat if it appears again.
5. Layer shift in X or Y axis:
- Check for hard movement on both directions.
- Increase Vref with 0.05V on the affected axis stepper driver. Repeat if it appears again.

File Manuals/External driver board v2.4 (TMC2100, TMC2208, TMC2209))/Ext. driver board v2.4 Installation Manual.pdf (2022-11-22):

## MK2(S) External Driver Board v2.4 Installation Manual

Thanks for supporting this project! I’ll try to guide you as best as I can, but I will not go to the simple details as how to place the nuts on their place and put together a box, I assume you’re good enough to do this.

Here’s two important things to know before proceeding with this mod:

1. By soldering on the back of your mini-rambo you’re practically voiding your prusa warranty!
2. I take no responsibility if you mess this modification up and/or damage your printer. You need to have basic soldering skills. Do at your own risk, or get someone more experienced to do it for you!

Let’s start:
First you need to supply power to the board. You disassemble the original PSU plastic cover and take it out just a little up so you can connect the power leads to it:

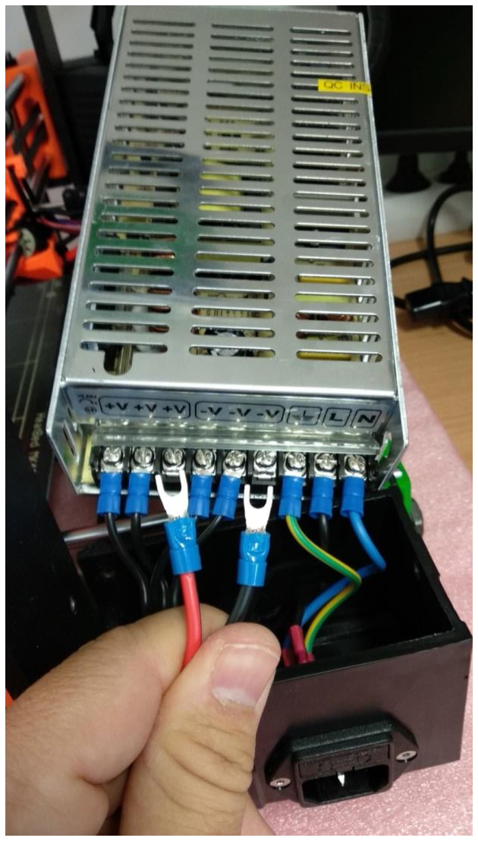
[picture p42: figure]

There’s a hole on the bottom left of the PSU plastic cover where all cables enter, put the new cable through there and connect to the PSU as shown (red is +V and black is –V):

Assemble back the PSU and route the wires with the original power wires to the mini-Rambo box.

Next is soldering the data wires to the mini-Rambo board.
The data cable has 8 wires and they are counted like this:

8 7 6 5 4 3 2 1

Wire 1

Wires description:

The wire on the side of the blue power connector is always wire number 1 (cable color could be red or grey)

1. X-EN - has to be soldered to XEN pad on the mini Rambo
2. X-STEP – has to be soldered to XSTEP pad on the mini Rambo
3. X-DIR – has to be soldered to XDIR pad on the mini Rambo
4. Y-EN – has to be soldered to YEN pad on the mini Rambo
5. Y-STEP - has to be soldered to YSTEP pad on the mini Rambo
6. Y-DIR - has to be soldered to YDIR pad on the mini Rambo
7. VCC - has to be soldered to +5V pad on the mini Rambo
8. GND - has to be soldered to GND pad on the mini Rambo

Unfortunately you will have to solder all 8 wires to the back of the mini-rambo.

Carefully peel off all 8 wires of the data cable almost to the end of the cable. Length should be enough to reach the solder points on the mini-rambo. Tin all wire ends and cut the excess wire so that you end up with very short tinned end.

In order to solder the wires you’ll have to unplug all cables and take the mini-rambo out of the box. Solder all wires on the back as shown below. (open the high res picture from the folder for clearer view)


Route all wires down and secure them with some hot silicone. This will prevent cutting the wires from vibrations etc.

Next you’ll have to solder the jumpers on the bottom of the ext. board according to the drivers/modes you want to use.

I suggest you use the TMC2208 or TMC2209 as they have a number of advantages over TMC2100. You can read more here: https://vmod.wordpress.com/2018/06/04/ext-driver-board-with-tmc2208/

There’s a quick cheat table on the right side of the ext. board on which jumpers to solder:


Here’s the combinations for the TMC drivers:

TMC2208 / TMC2209 (solder all jumpers on the left side for StealthChop2 mode):


TMC2100 (solder JY1 and JX1 on the right side for SpreadCycle or leave all unsoldered for StealthChop which is the recommended mode):


Be careful not to short the other side of the jumpers when soldering! You WILL DAMAGE your mini-Rambo if you short both sides of any jumper!!

You can now assemble the mini-rambo back in the original box with all cables plugged back (except for X and Y motor cables). Replace the bottom two screws with longer ones, remove the nuts from the original box and place them on the Ext. driver board box. (I assume you have printed it, https://www.thingiverse.com/thing:2777899) Assemble the external driver board in the new box and secure the box to the original box with the two longer screws. (note: If you’re installing a voltmeter place it first before the external board, otherwise it won’t be possible later) You should now have all data wires soldered, mini-rambo back in place with all cables plugged and the new box secured on the outside.

You can now plug motor cables for X and Y motors in the external driver board:

Y-mot.; X-mot.

Next screw the power cables to the POWER socket, red is +12V, black is GND:


You can plug the optional 40x40 Noctua fan in the FAN socket on the board.


Next connect the Data connector to the external driver board so that wire number 1 is on the POWER side:

*Note – picture is from v2.3 but it’s the same wiring for v2.4
Now that you have all the wiring done you can plug the drivers to their places oriented with the pot trimmer/pot hole on the left side (TMC2208 have the pot on the bottom, so look for the hole to the pot). Example of TMC2100s plugged:

Wire 1 is on
the POWER
side

Check all wiring again before turning the printer on. Place bigger heatsinks if available on the drivers.

After powering on don’t rush to print, follow this first:

1. Check X and Y motors movement directions (Settings -> Move axis). Move them from the menu one by one. Are directions correct?
2. Check if “Disable steppers” is working fine.
3. Now you have to set Vref on the drivers, but it depends on what bearings you have on your Prusa. If you have LM8UU original bearings set Vref to 0.81V. If you use IGUS I recommend to set Vref to 1V or replace them back with the original metal ones, because IGUS will cause more friction and may cause layer shifting…
4. Set the Vref voltages on both drivers to 0.81 V with multimeter, here’s how:
- Put the multimeter to small DC voltage range (2 – 5 volts, etc.)
- Place the Black lead to GND on the POWER socket.
- Place the Red lead to the pot center (TMC2100) or at the Vref pin (TMC2208 / TMC2209)

TMC2208 Vref pin

- Be careful not to touch anything else with the Red multimeter lead!
- Rotate the pot with plastic screwdriver slowly clockwise so that voltage gets to 0.81 V:


- Stepper motors will get hot during print, but this seems to be normal for the TMC drivers. Using plastic screwdriver will ensure you’re not going to short anything. I’ve already burned one driver with metal screwdriver…
5. Do XYZ calibration, and first layer calibration. (http://www.youtube.com/watch?v=JqH41K2vq0g&t=9m50s)

X and Y stepper movement should be normal and quieter than before.

Before making the first print assemble the box cover with the optional Noctua fan. Cooling the drivers will be your second assurance for normal operation and no layer shifting.

Finally – enjoy your new silent printer! Happy printing!

Basic troubleshooting:

### 1. Strange noise during mesh bed levelling or high speeds:

Read this: https://vmod.wordpress.com/2018/07/09/tmcs-and-rubbing-sound-during-mesh-bed-levelling/ (https://vmod.wordpress.com/2018/07/09/tmcs-and-rubbing-sound-during-mesh-bed-levelling/)

### 2. If X or Y motors are not moving you have a couple of reasons why:

- Check connection of wire 2 for X and wire 5 for Y.
- Check connection of wire 1 for X and wire 4 for Y.
- There’s no power to the external board, check the voltage on the power socket with multimeter (Red lead to 12V and Black to GND).
- There’s no 5V power to the stepper drivers, check wires 7 and 8. check the voltage between them with multimeter, should read 5V)
- Vref is too low. Set Vref according to the manual above.
- The stepper driver is faulty. I’ve seen this with some Chinese clones. Turn the printer off and swap the two TMCs. If now the other axis is not moving then you have either wiring problem or driver is faulty.
3. “Disable steppers” is not working:
- Check connection of wire 1 for X and wire 4 for Y

### 4. Motor is moving only in one direction despite what you command from

the LCD:
- Check connection of wire 3 for X and wire 6 for Y

### 5. XYZ calibration fails:

- Increase Vref with 0.05V on both stepper drivers. Repeat if it appears again.

### 6. Layer shift in X or Y axis:

- Check for hard movement on both directions.
- Increase Vref with 0.05V on the affected axis stepper driver. Repeat if it appears again.

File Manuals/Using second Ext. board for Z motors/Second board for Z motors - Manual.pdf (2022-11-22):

## Using second external driver (v2.3/v2.4) board for Z motors on MK2S/MK2.5


Ok, so you want it all? You want the Z motors to use external drivers, too? This guide is for the more advanced users as it requires more soldering and more wire connections. After you do it you’ll have the advantage of quiet Z motors and also running them with two separate drivers instead of running them with one as on the original Rambo board.

So here’s a short guide how to do it.

There’s two important things to know before proceeding with this mod:

1. By soldering on the back of your mini-rambo you’re practically voiding your prusa warranty!
2. I take no responsibility if you mess this modification up and/or damage your printer. You need to have basic soldering skills. Do at your own risk, or get someone more experienced to do it for you!

You will need a second external driver board kit. Following my previous manuals, you may already have soldered the Data cable from the first ext. board to the mini-Rambo. If not, you can do them all at once. Here’s where to solder the second Data cable:


You just solder each pair of wires to the corresponding pad on the board, as described on the picture above. Secure the data wire next to solder points and at the end with hot silicone to avoid any disconnections due to vibrations etc.

Please pay attention how you count the wires as explained on the next page.

Wire 1

The data cable has 8 wires and they are counted like this:

Wires description:

The wire on the side of the blue power connector is always wire number 1 (cable color could be red or grey)

1. X-EN - has to be soldered to ZEN pad on the mini Rambo
2. X-STEP – has to be soldered to ZSTEP pad on the mini Rambo
3. X-DIR – has to be soldered to ZDIR pad on the mini Rambo
4. Y-EN – has to be soldered to ZEN pad on the mini Rambo
5. Y-STEP - has to be soldered to ZSTEP pad on the mini Rambo
6. Y-DIR - has to be soldered to ZDIR pad on the mini Rambo
7. VCC - has to be soldered to +5V pad on the mini Rambo
8. GND - has to be soldered to GND pad on the mini Rambo

Once you have the second Data cable soldered you can proceed assembling back the mini-rambo and reconnecting all the wires.

Next thing to do is get 12V to supply the second board. You’ll have to cut the power cable for the first ext. driver board and connect the second power cable to it. Solder them together and insulate them good. Here’s the schematic:


Next thing to do is just connect the two Z motor wires to the connectors on the second external driver board (no matter which goes where, both do the same).

Next are jumpers, for ext. board v2.3 follow this:

If you’ll be using TMC2100 you’re ok to plug them in the board and continue to adjust VRef.

If you’ll be using TMC2208 please desolder the two jumpers on the ext. driver board and solder the bridge wire on the drivers as described in the TMC2208 manual here:
https://drive.google.com/open?id=1JyrXp6G7wkWhmKt6thdGa5ojQeswQbob

WARNING! If you don’t follow the above manual for TMC2208 you WILL DAMAGE your Rambo mainboard! So please read it and do it carefully!!!

For v2.4 of the ext. board follow this:

There’s a table on the right side of the board on which jumpers to solder:


Here’s the combinations for the TMC drivers:

TMC2208 (solder all jumpers on the left side for Stealthchop2 mode):


TMC2100 (solder JY1 and JX1 on the right side for Spreadcycle or leave all unsoldered for Stealthchop which is the recommended mode):


Be careful not to short the other side of the jumpers when soldering! You WILL DAMAGE your mini-Rambo if you short both sides of any jumper!!

I suggest you use the TMC2208 as they have a number of advantages over TMC2100. You can read more here: https://vmod.wordpress.com/2018/06/04/ext-driver-board-with-tmc2208/

Check all wiring again and power on the printer. Before trying to do anything you’ll have to set VRef on both TMCs as you did with the first board, just follow that manual and set Vref to 0.75V for both Z motors. It should be enough to move freely the motors.

Previous manuals can be found here:

https://drive.google.com/open?id=1o_A4ZHai253kLMRttBMnLbEIv-KRri8t

Lastly just try to move the Z axis via the Menu. If all looks good do the Z calibration again and enjoy the silence!

Happy printing!

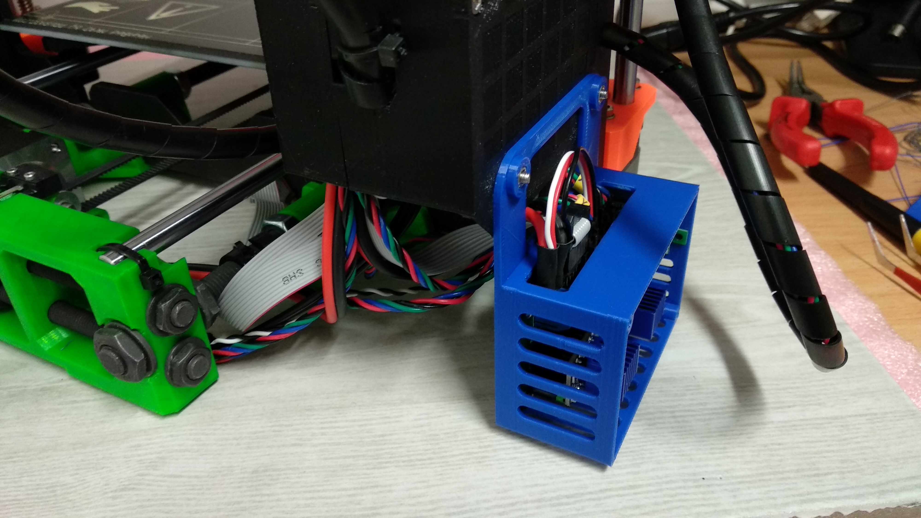
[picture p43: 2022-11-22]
Manuals/External driver board v2.4 (TMC2100, TMC2208, TMC2209))/high res pics/IMG_20180121_210024.jpg

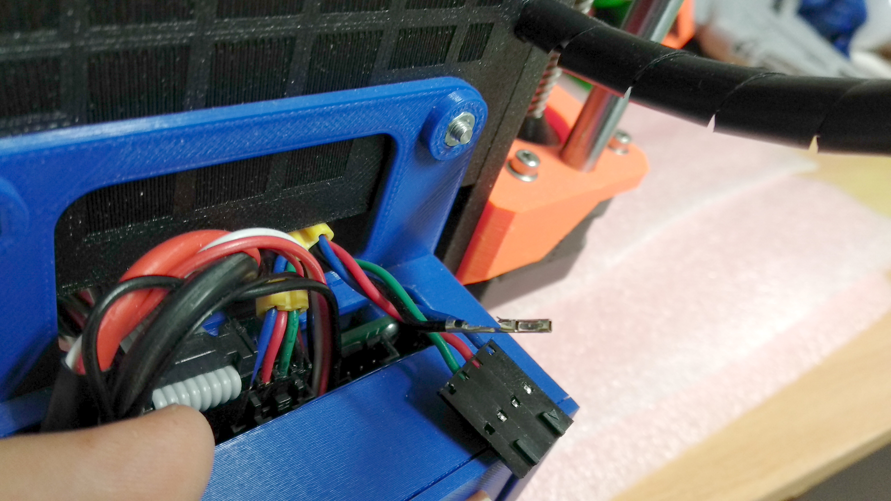
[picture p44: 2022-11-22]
Manuals/External driver board v2.1 with MK2.5/high res pics/IMG_20180408_231225.jpg

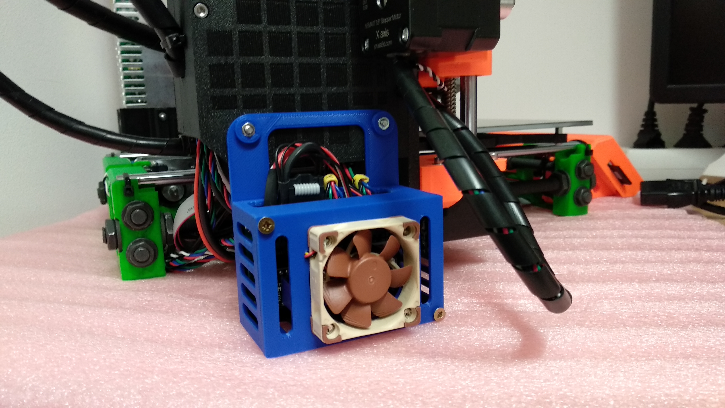
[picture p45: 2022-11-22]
Manuals/External driver board v2.1 with MK2S/High res pics/IMG_20180124_002404.jpg

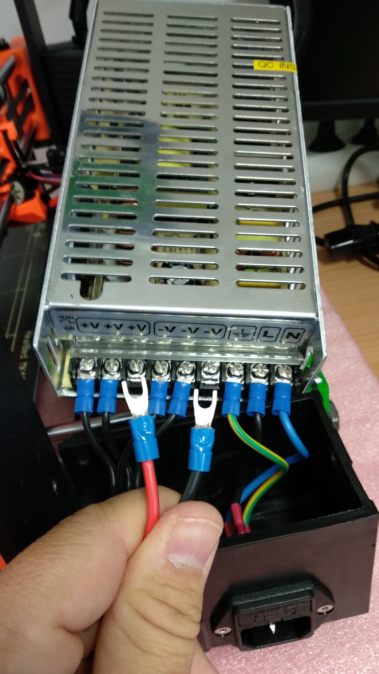
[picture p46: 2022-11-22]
Manuals/External driver board v2.3/high res pics/IMG_20180204_120422.jpg

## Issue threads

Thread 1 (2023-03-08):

Part List

ATOG2074, 2023-03-08:
I know i'm a little late to the party only i did not use my printer a lot because of the noise it makes now i found this GitHub

now i can order 5 PCB's at PCBWay for only 10euro i don't know what parts i need to solder on the board is there a list so i can order the parts.

- Connectors
- Capacitors
- Resistors

zauberstuhl, 2024-01-03:
As far as I can tell:

* 2 x 10k Ohm resistor
* 2 x 100uF capacitors
* Molex connector
* Pheonix power connector

toto99303, 2024-01-05:
Hello, sorry for the late reply, I've added a BOM to the main readme page. Have fun!

toto99303, 2024-01-05:
Closing.

toto99303, 2024-01-05:
Hello, sorry for the late reply, I've added a BOM to the main readme page. Have fun!

Closed 2024-01-05.

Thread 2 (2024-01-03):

Selling PCB Boards

zauberstuhl, 2024-01-03:
Hi there,

not sure if this is the right 'forum' for this, but I have ordered a couple of PCBs based on the latest version.

Contact me (lukas AT matt DOT wf) if you need one. As long as you pay the shipping :)

Also #1 would be extremely helpful @toto99303  .

Thanks for your work!

toto99303, 2024-01-05:
No need for PCBs, thanks and have fun! BOM is added to the main page.

Closed 2024-01-05.

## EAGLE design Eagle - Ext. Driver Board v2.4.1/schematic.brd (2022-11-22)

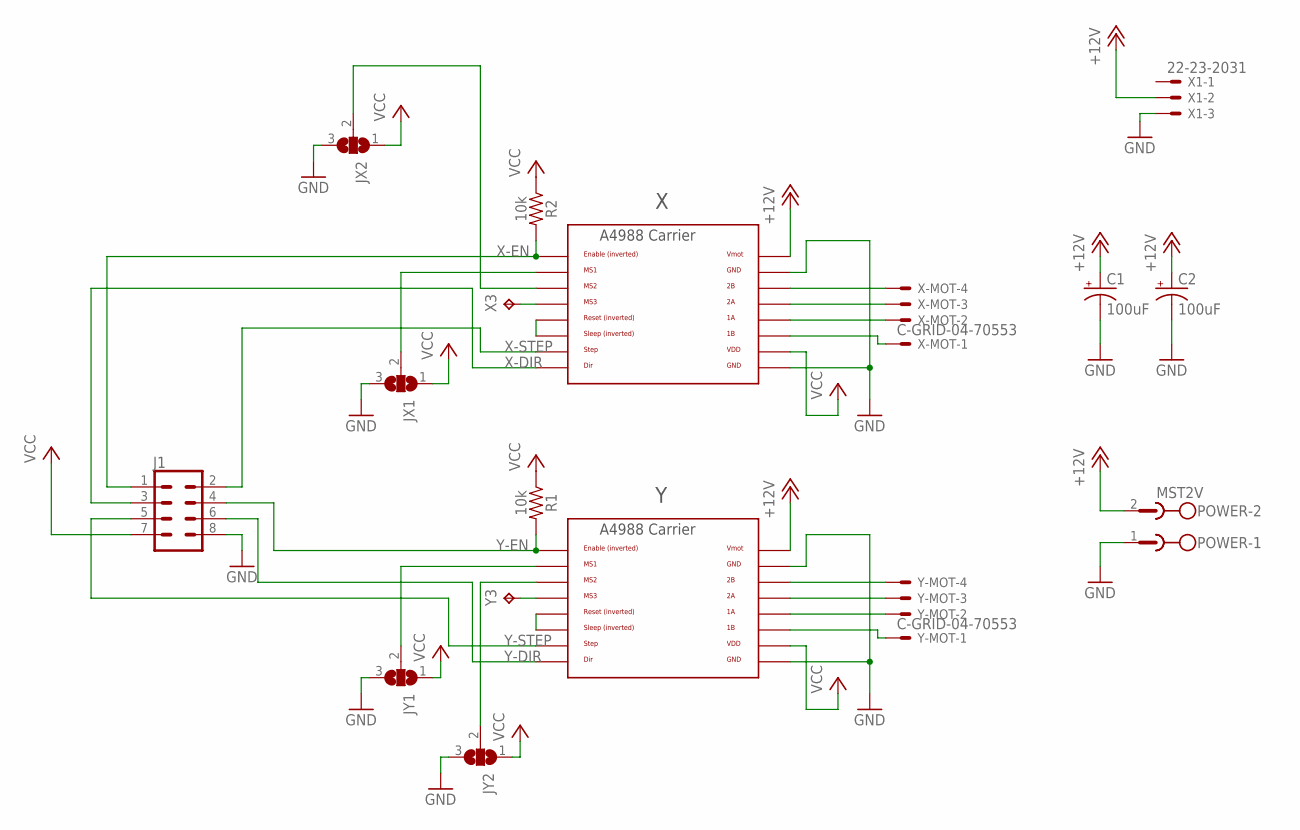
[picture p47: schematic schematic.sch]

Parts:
C1, C2: 100uF; CPOL-RADIAL-2.5MM-6.5MM
J1: CONN_04X2; 2X4
JX1, JX2: SJ2W; SJ_2
JY1, JY2: SJ2W; SJ_2
POWER: MST2V; MSTBV2
R1, R2: 10k; AXIAL-0.3
U$1, U$4: A4988BREAKOUT
X1: 22-23-2031
X3: TPB1,27; B1,27
X-MOT: C-GRID-04-70553; 70553-04
Y3: TPB1,27; B1,27
Y-MOT: C-GRID-04-70553; 70553-04

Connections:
+12V: C1.1 (+), C2.1 (+), POWER.2, U$1.VMOT, U$4.VMOT, X1.2
GND: C1.2 (-), C2.2 (-), J1.8, JX1.3, JX2.3, JY1.3, JY2.3, POWER.1, U$1.GND, U$1.GND@0 (GND), U$4.GND, U$4.GND@0 (GND), X1.3
unnamed: JY2.2, U$4.MS2
unnamed: U$4.MS3, Y3.TP
unnamed: U$4.2B, Y-MOT.4
unnamed: U$4.2A, Y-MOT.3
unnamed: U$1.RST, U$1.SLP (SLEEP)
unnamed: U$1.2B, X-MOT.4
unnamed: U$1.2A, X-MOT.3
unnamed: U$4.RST, U$4.SLP (SLEEP)
unnamed: U$1.1A, X-MOT.2
unnamed: U$4.1A, Y-MOT.2
unnamed: U$4.1B, Y-MOT.1
unnamed: U$1.1B, X-MOT.1
unnamed: JX2.2, U$1.MS2
unnamed: U$1.MS3, X3.TP
unnamed: JX1.2, U$1.MS1
unnamed: JY1.2, U$4.MS1
VCC: J1.7, JX1.1, JX2.1, JY1.1, JY2.1, R1.P$1 (1), R2.P$1 (1), U$1.VDD, U$4.VDD
X-DIR: J1.3, U$1.DIR
X-EN: J1.1, R2.P$2 (2), U$1.EN
X-STEP: J1.2, U$1.STEP
Y-DIR: J1.6, U$4.DIR
Y-EN: J1.4, R1.P$2 (2), U$4.EN
Y-STEP: J1.5, U$4.STEP

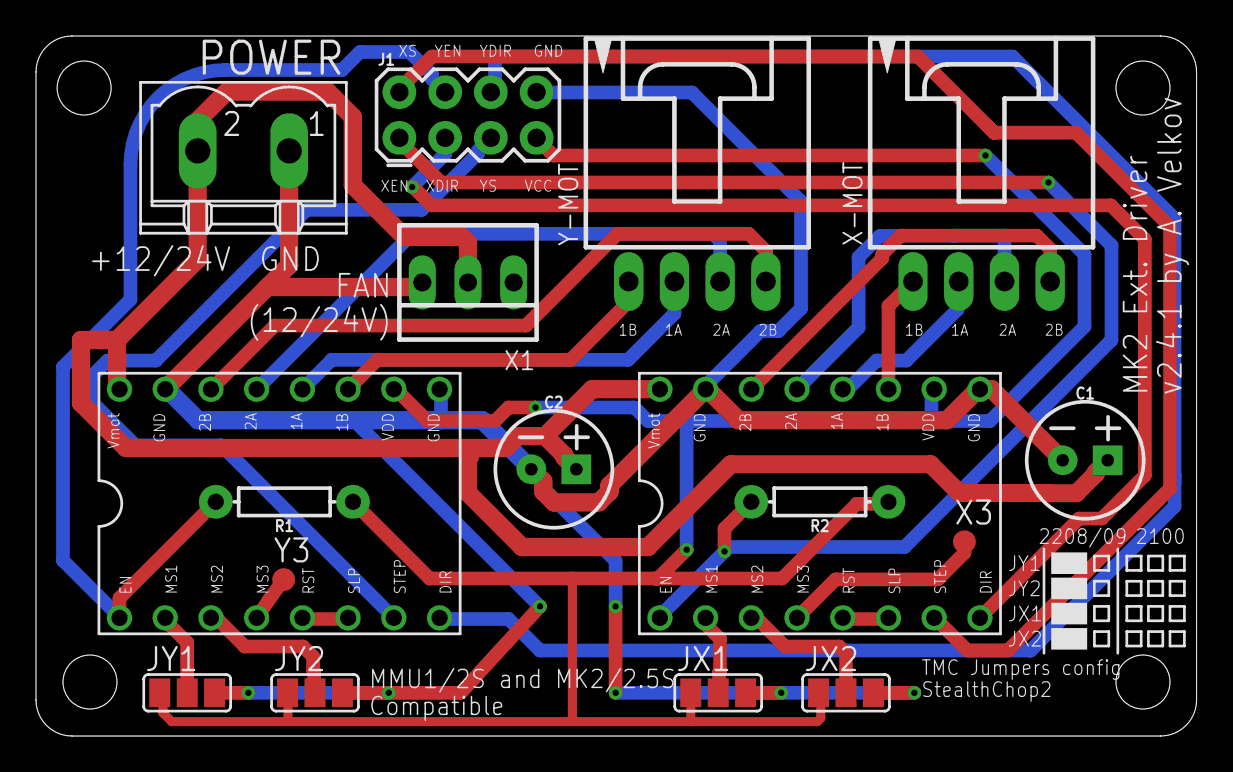
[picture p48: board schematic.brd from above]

Board: 2 copper layers, 64.5 x 38.9 mm, 17 parts (0 on the bottom side), 25 nets.

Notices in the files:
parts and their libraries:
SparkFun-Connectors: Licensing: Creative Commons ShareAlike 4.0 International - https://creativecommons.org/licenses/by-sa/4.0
